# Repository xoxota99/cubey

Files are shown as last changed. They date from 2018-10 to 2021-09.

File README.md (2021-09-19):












# cubey
A Raspberry pi-based Rubik's Cube solving robot.

## Thanks
All credit goes to Jay Flatland, and his [HighFrequencyTwister](https://github.com/jayflatland/HighFrequencyTwister) as the inspiration for this project. This build is just a ghetto version of Jay's project, with a bit of cleaned up documentation, EAGLE files for the relevant PCB, a BOM, and extraneous (to me) stuff removed.

## Hardware
I'm using all the same hardware and 3D-printed parts as [HighFrequencyTwister](https://github.com/jayflatland/HighFrequencyTwister) , but replaced the PC / Arduino combination with a single Raspberry pi. 

I've also created a [custom PCB](https://oshpark.com/shared_projects/dzYt5cpy) to tidy up the wiring of the DRV8825 carrier boards. It sits where a Raspberry pi hat would sit, but definitely does NOT conform to the RPI Hat specification (no cutouts for display connector, no EEPROM for board identification, etc.)

## Software
cubey uses the python implementation of the [kociemba solver](https://github.com/muodov/kociemba), and [piGPIO](https://github.com/joan2937/pigpio) for stepper motor control. Cubey uses a single camera for Cube State estimation, which simplifies calibration, but impacts speed. Cubey definitely *won't* set any world speed records.

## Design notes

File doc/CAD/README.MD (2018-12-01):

STL files (for 3D printing) are in this folder. For the original Fusion 360 files:
- Bottom frame (5 motors): https://a360.co/2QQcA4i
- Top frame (1 motor): https://a360.co/2QOjB5D
- Camera mount / bracket: https://a360.co/2Py3g8A 
- Drill Template: https://a360.co/2qSi3vY
- Stepper Motor Drive Bit: https://a360.co/2PEiVTS

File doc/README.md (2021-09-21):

# Setting Up your Raspberry Pi
These instructions are for Ubuntu 21.04 or later on Raspberry Pi. Other than service setup, they should be applicable to any debian-based, reasonably recent OS (such as Raspbian, or whatever they're calling it now).

## The Basics
Install Ubuntu Server 21.04 or later: https://ubuntu.com/tutorials/how-to-install-ubuntu-on-your-raspberry-pi#1-overview 

SSH into your new, up-and-running RPi using "ubuntu/ubuntu". Change the password.

Create a new user (here we're creating a user "cubey"):

    sudo adduser cubey
    sudo adduser cubey sudo

(Optional) Enable passwordless login: https://linuxize.com/post/how-to-setup-passwordless-ssh-login/ 

SSH into your RPi as the new user you just created.

**Slow SSH logins?** Disable PAM auth: change `UsePAM` from `yes` to `no` in */etc/ssh/sshd_config*

    UsePAM no

(Optional) change the hostname in */etc/hostname*

(Optional) set the timezone: `sudo dpkg-reconfigure tzdata`

(Optional) install zsh: `sudo apt install zsh`

(Optional) set zsh as your default shell: `chsh -s $(which zsh)`

(Optional) install oh-my-zsh: `sh -c "$(curl -fsSL https://raw.github.com/ohmyzsh/ohmyzsh/master/tools/install.sh)"`

Update to latest of everything: 

    sudo apt update
    sudo apt dist-upgrade

Now would be a good time to reboot the RPi (using `sudo reboot`), and reconnect.

## Install Python (3.9):

    sudo apt install -y build-essential python3-setuptools software-properties-common python3.9 python3.9-venv python3.9-dev python3-pip v4l-utils

Set python 3.9 as the default for python3

    cd /usr/bin

    sudo rm aarch64-linux-gnu-python3-config pdb3 pydoc3 pygettext3 python3 python3-config

    sudo sh -c 'ln -s aarch64-linux-gnu-python3.9-config aarch64-linux-gnu-python3-config && \
    ln -s pdb3.9 pdb3 && \
    ln -s pydoc3.9 pydoc3 && \
    ln -s pygettext3.9 pygettext3 && \
    ln -s python3.9 python3 && \
    ln -s python3.9-config python3-config'

## Install OpenCV
    sudo apt install -y python3-opencv

## Install GPIO support
    sudo apt install python3-rpi.gpio python3-lgpio

## Install PIGPio
    cd
    wget https://github.com/joan2937/pigpio/archive/master.zip
    unzip master.zip
    cd pigpio-master
    make
    sudo make install
    sudo touch /lib/systemd/system/pigpiod.service

Add the following to /lib/systemd/system/pigpiod.service:

    [Unit]
    Description=Daemon required to control GPIO pins via pigpio
    [Service]
    ExecStart=/usr/local/bin/pigpiod
    ExecStop=/bin/systemctl kill -s SIGKILL pigpiod
    Type=forking
    [Install]
    WantedBy=multi-user.target

Setup pigpio to run at startup:

    sudo systemctl enable pigpiod

Reboot again, and reconnect.

## Install cubey
    cd
    git clone https://github.com/xoxota99/cubey.git

## Install cubey dependencies: 
    sudo pip install -r cubey/requirements.txt

This includes:
* The [kociemba](https://pypi.org/project/kociemba/) solver library
* [flask](https://flask.palletsprojects.com/en/2.0.x/) web development framework
* [pillow](https://pillow.readthedocs.io/en/stable/) image library.
* [greenlet](https://greenlet.readthedocs.io/en/latest/) concurrent process library
* Prebuilt [OpenCV libraries](https://pypi.org/project/opencv-python/) for python
* Prebuilt [OpenCV addons](https://pypi.org/project/opencv-contrib-python/) for python

## Enable shutdown button and power LED (Optional)
In */boot/firmware/config.txt*, add the following:

    dtoverlay=gpio-poweroff,gpiopin=14
    dtoverlay=gpio-shutdown,gpio_pin=4,active_low=1

and comment out `enable_uart=1`

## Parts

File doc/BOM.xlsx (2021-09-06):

Qty | Description | Link | Unit Price | Total*
1 | Raspberry PI 3 Model B | https://www.amazon.com/dp/B01CD5VC92 | $34.99 | $34.99
2 | Stepper Motor 3-pack | https://www.amazon.com/dp/B00Y2HGJV6 | $26.99 | $53.98
2 | DRV8825 Stepper Motor Driver 5-pack | https://www.amazon.com/dp/B075XH1TSJ | $11.99 | $23.98 | *bulk packs of 5.
1 | 12V Power supply | https://www.amazon.com/dp/B07557XMDQ | $16.80 | $16.80
1 | Power socket | https://www.amazon.com/dp/B06XNMT3WL | $7.49 | $7.49
2 | USB Camera | https://www.amazon.com/dp/B01N07O9CQ | $42.99 | $85.98
1 | AC Power cord | https://www.amazon.com/dp/B07D6MT4L9 | $8.99 | $8.99
1 | Cable wrap / sleeve | https://www.amazon.com/dp/B01MT81WNF | $6.60 | $6.60
1 | Rubik's Cube | https://www.amazon.com/dp/B06XH9Y2XJ | $7.89 | $7.89
1 | 40mm Case fan | https://www.amazon.com/dp/B01CZFUOD0 | $13.98 | $13.98
1 | 40mm fan finger guard grill | https://www.amazon.com/dp/B00D7IH1OK | $5.99 | $5.99
1 | Pololu 5V, 2.5A Step-Down Voltage Regulator D24V22F5 | https://www.pololu.com/product/2858 | $8.95 | $8.95
1 | DRV8825 Stepper Motor PCB | https://oshpark.com/shared_projects/E8F8le0Q | $37.50 | $37.50
1 | Raspbery Pi HAT header | https://www.digikey.com/product-detail/en/te-connectivity-amp-connectors/2-215309-0/A106671-ND/2278517 | $6.12 | $6.12 | For Stepper motor PCB
6 | 100uf Capacitor | https://www.digikey.com/products/en?keywords=P5182-ND | $0.33 | $1.98 | For Stepper motor PCB
1 | terminal blocks 5-pack | https://www.adafruit.com/product/724 | $2.95 | $2.95 | For Stepper motor PCB
Total |  |  |  | $324.17
*Item totals do not include taxes, shipping, customs, etc. YMMV
In addition to the above, you'll ned to 3D-print the actual robot frame.
You'll also need basic tools, soldering iron, screws, wire, etc.
I also laser-cut an acrylic sheet to form the case. That was about $40. Any reasonably sturdy box should do the trick.

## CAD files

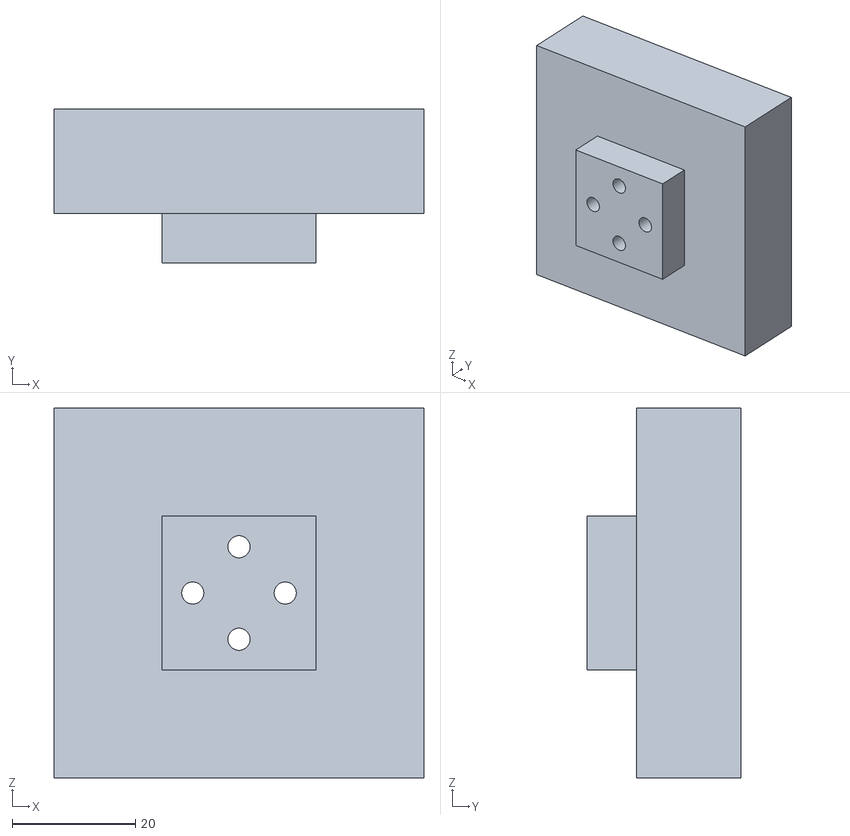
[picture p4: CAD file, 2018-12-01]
doc/CAD/drill_template.stl
60.0 x 25.0 x 60.0

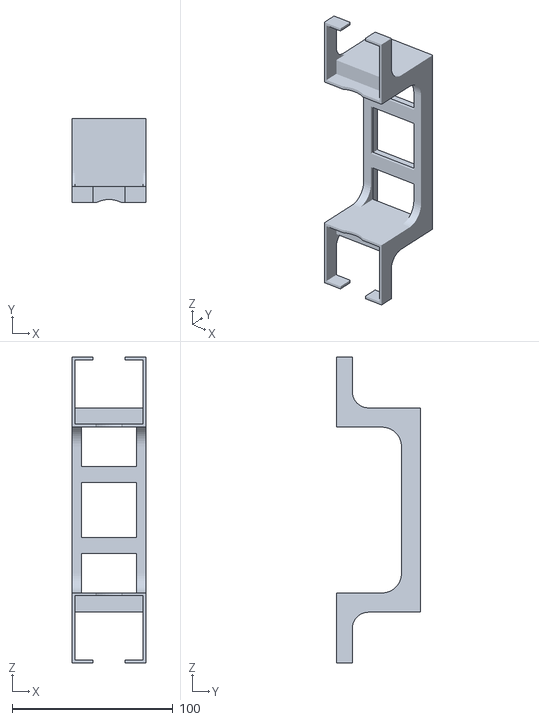
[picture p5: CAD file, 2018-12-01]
doc/CAD/frame_top.stl
46.0 x 52.5 x 190.2

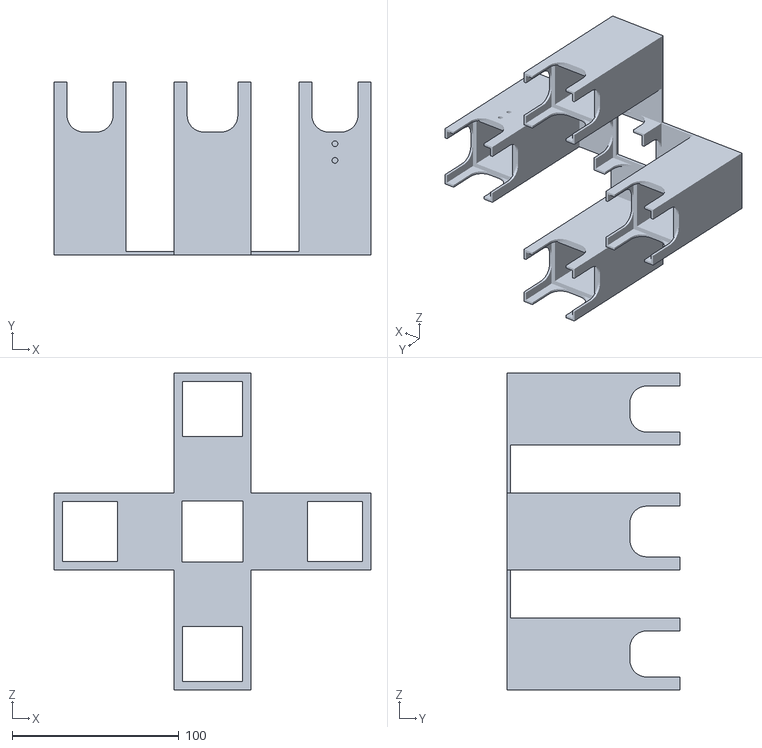
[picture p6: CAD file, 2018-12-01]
doc/CAD/frame_bottom.stl
190.0 x 103.7 x 190.0

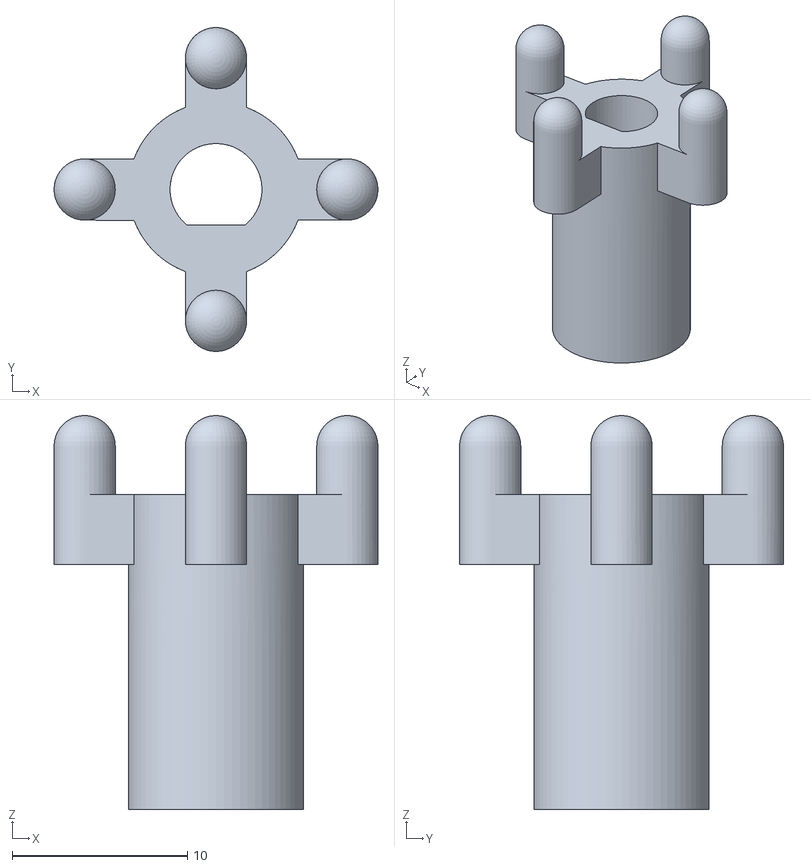
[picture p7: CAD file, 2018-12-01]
doc/CAD/motor_drive_bit.stl
18.5 x 18.5 x 22.5

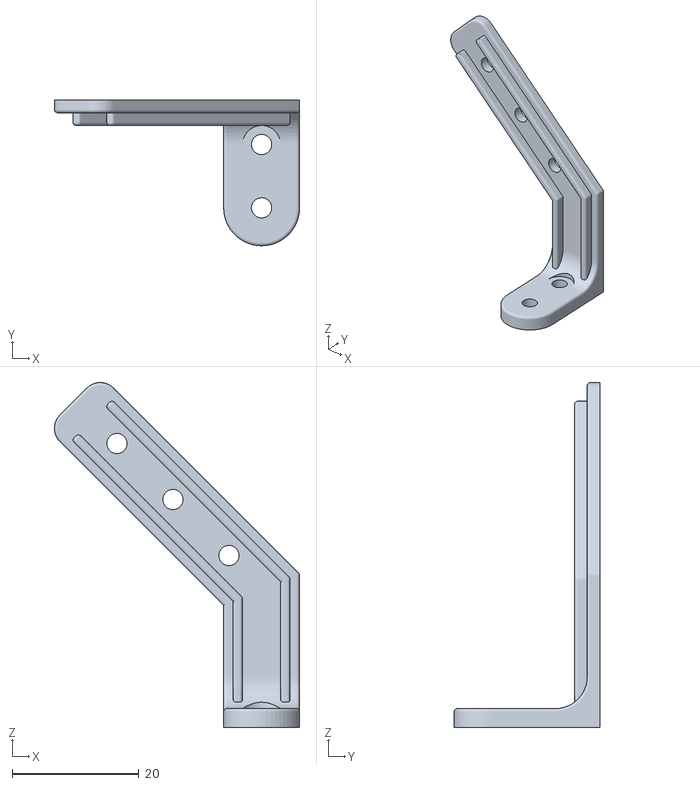
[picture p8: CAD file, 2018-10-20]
doc/CAD/camera_mount.stl
38.7 x 23.0 x 54.5

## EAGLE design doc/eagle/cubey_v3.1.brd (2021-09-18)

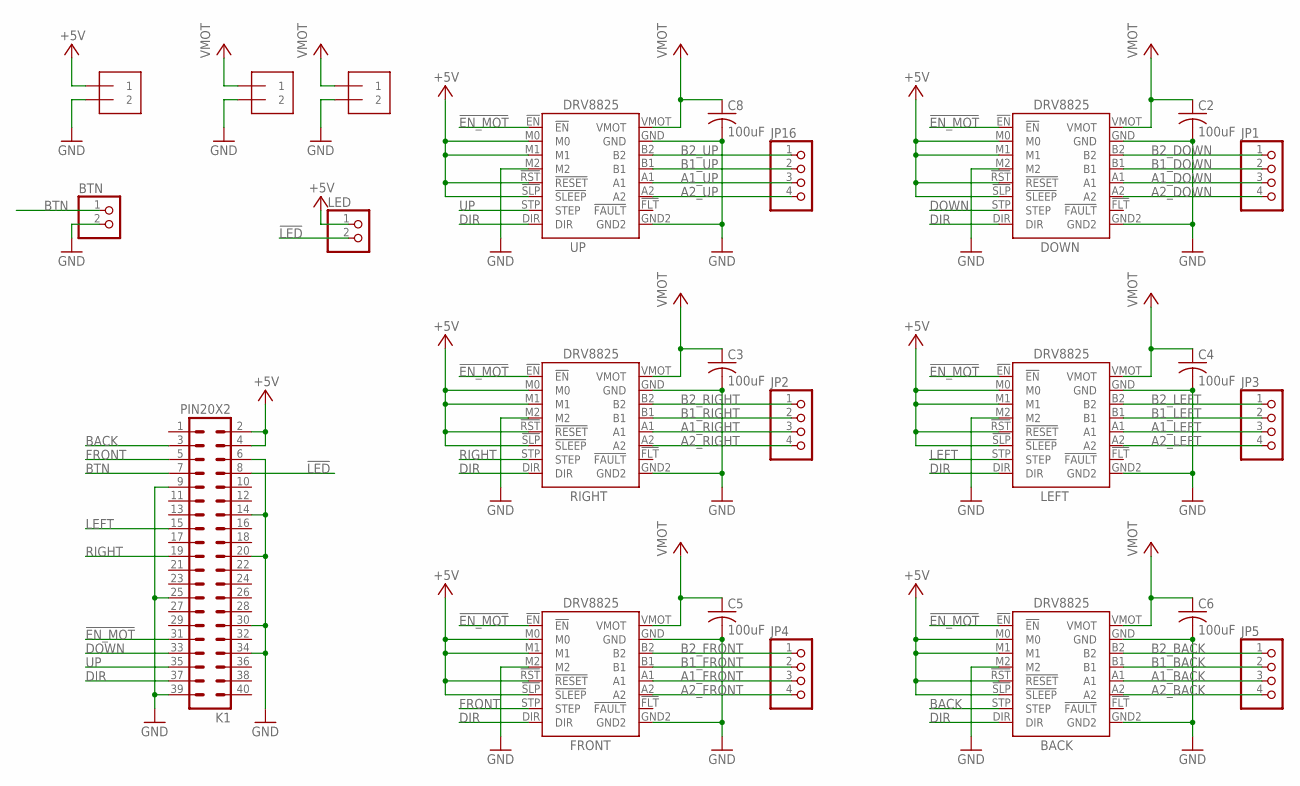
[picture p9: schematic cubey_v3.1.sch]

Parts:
5V_PWR: 1X2-3.5MM
BACK: DRV_8825_SOCKET; DRV_8825_DIP
BTN: PINHD-1X2; 1X02
C2, C3, C4, C5, C6, C8: 100uF; C025-025X050
DOWN: DRV_8825_SOCKET; DRV_8825_DIP
FRONT: DRV_8825_SOCKET; DRV_8825_DIP
JP1, JP2, JP3, JP4, JP5, JP16: PINHD-1X4; 1X04
K1: PIN20X2; PIN_20X2
LED: PINHD-1X2; 1X02
LEFT: DRV_8825_SOCKET; DRV_8825_DIP
MOT_PWR, MOT_PWR1: 1X2-3.5MM
RIGHT: DRV_8825_SOCKET; DRV_8825_DIP
UP: DRV_8825_SOCKET; DRV_8825_DIP

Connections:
!EN_MOT: BACK.!EN, DOWN.!EN, FRONT.!EN, K1.31, LEFT.!EN, RIGHT.!EN, UP.!EN
!LED: K1.8, LED.2
+5V: 5V_PWR.1, BACK.!RST (!RESET), BACK.!SLP (!SLEEP), BACK.M0, BACK.M1, DOWN.!RST (!RESET), DOWN.!SLP (!SLEEP), DOWN.M0, DOWN.M1, FRONT.!RST (!RESET), FRONT.!SLP (!SLEEP), FRONT.M0, FRONT.M1, K1.2, K1.4, LED.1, LEFT.!RST (!RESET), LEFT.!SLP (!SLEEP), LEFT.M0, LEFT.M1, RIGHT.!RST (!RESET), RIGHT.!SLP (!SLEEP), RIGHT.M0, RIGHT.M1, UP.!RST (!RESET), UP.!SLP (!SLEEP), UP.M0, UP.M1
A1_BACK: BACK.A1, JP5.3
A1_DOWN: DOWN.A1, JP1.3
A1_FRONT: FRONT.A1, JP4.3
A1_LEFT: JP3.3, LEFT.A1
A1_RIGHT: JP2.3, RIGHT.A1
A1_UP: JP16.3, UP.A1
A2_BACK: BACK.A2, JP5.4
A2_DOWN: DOWN.A2, JP1.4
A2_FRONT: FRONT.A2, JP4.4
A2_LEFT: JP3.4, LEFT.A2
A2_RIGHT: JP2.4, RIGHT.A2
A2_UP: JP16.4, UP.A2
B1_BACK: BACK.B1, JP5.2
B1_DOWN: DOWN.B1, JP1.2
B1_FRONT: FRONT.B1, JP4.2
B1_LEFT: JP3.2, LEFT.B1
B1_RIGHT: JP2.2, RIGHT.B1
B1_UP: JP16.2, UP.B1
B2_BACK: BACK.B2, JP5.1
B2_DOWN: DOWN.B2, JP1.1
B2_FRONT: FRONT.B2, JP4.1
B2_LEFT: JP3.1, LEFT.B2
B2_RIGHT: JP2.1, RIGHT.B2
B2_UP: JP16.1, UP.B2
BACK: BACK.STP (STEP), K1.3
BTN: BTN.1, K1.7
DIR: BACK.DIR, DOWN.DIR, FRONT.DIR, K1.37, LEFT.DIR, RIGHT.DIR, UP.DIR
DOWN: DOWN.STP (STEP), K1.33
FRONT: FRONT.STP (STEP), K1.5
GND: 5V_PWR.2, BACK.GND, BACK.GND2, BACK.M2, BTN.2, C2.2, C3.2, C4.2, C5.2, C6.2, C8.2, DOWN.GND, DOWN.GND2, DOWN.M2, FRONT.GND, FRONT.GND2, FRONT.M2, K1.6, K1.9, K1.14, K1.20, K1.25, K1.30, K1.34, K1.39, LEFT.GND, LEFT.GND2, LEFT.M2, MOT_PWR.2, MOT_PWR1.2, RIGHT.GND, RIGHT.GND2, RIGHT.M2, UP.GND, UP.GND2, UP.M2
LEFT: K1.15, LEFT.STP (STEP)
RIGHT: K1.19, RIGHT.STP (STEP)
UP: K1.35, UP.STP (STEP)
VMOT: BACK.VMOT, C2.1, C3.1, C4.1, C5.1, C6.1, C8.1, DOWN.VMOT, FRONT.VMOT, LEFT.VMOT, MOT_PWR.1, MOT_PWR1.1, RIGHT.VMOT, UP.VMOT

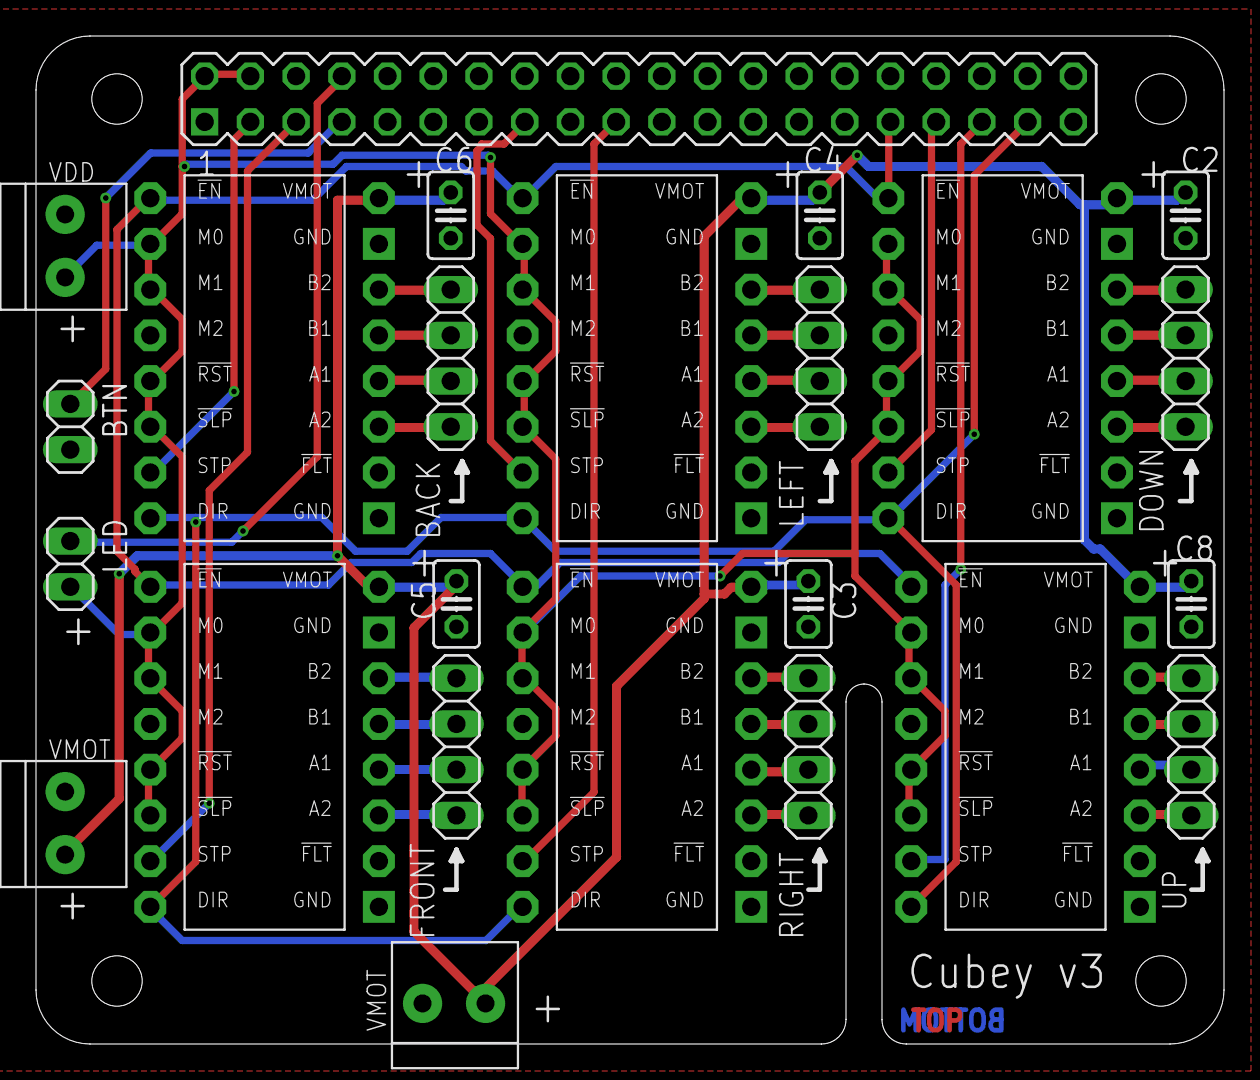
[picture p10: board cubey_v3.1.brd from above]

Board: 2 copper layers, 66.0 x 56.0 mm, 24 parts (0 on the bottom side), 37 nets.

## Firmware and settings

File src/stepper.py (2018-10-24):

from __future__ import division
from time import sleep
import math
import pigpio
from config import cfg

# We are only spinning one motor at a time, so only need one DIR pin.
# (All motors are on the same DIR bus).
pins = cfg['stepper']['pins']
DIR = pins['dir']                # Direction GPIO Pin

UP = pins['up']                  # UP face stepper
RIGHT = pins['right']            # RIGHT face stepper
FRONT = pins['front']            # FRONT face stepper
DOWN = pins['down']              # DOWN face stepper
LEFT = pins['left']              # LEFT face stepper
BACK = pins['back']              # BACK face stepper
DISABLE = 0

if 'disable' in pins:
    DISABLE = pins['disable']

MOTOR_PIN = [UP, RIGHT, FRONT, DOWN, LEFT, BACK]  # Step GPIO Pins
STEP_NAME = ["U", "R", "F", "D", "L", "B"]
STEP_MAP = {
    "U": UP,
    "R": RIGHT,
    "F": FRONT,
    "D": DOWN,
    "L": LEFT,
    "B": BACK
}
RPM = cfg['stepper']['rpm']  # complete revolutions (360 deg.) per minute
# steps per revolution (varies by motor)
STEPS_PER_REVOLUTION = cfg['stepper']['steps_per_rev']
STEPS_PER_DEGREE = STEPS_PER_REVOLUTION / 360.0
STEP_FACTOR = cfg['stepper']['step_factor']
# PULSE_LENGTH_US = 1000000 // (STEPS_PER_REVOLUTION * RPM // 60)
# e.g. 4 revolutions per second = 800 steps per second.
# 800 steps per second = one step every 1250 uS.

MOVE_DELAY = cfg['stepper']['move_delay']

CW = 1
CCW = 0

HERTZ = cfg['stepper']['hertz']

pi = None       # pigpio reference
is_init = False


def _init(force=False):
    """
    _initialize stepper motor frequency / PWM ramps for 90 and 180-degree turns
    """
    global is_init, pi

    # Connect to pigpiod daemon
    pi = pigpio.pi()
    sleep(0.001)

    if force or not is_init:
        if DISABLE:
            pi.set_mode(DISABLE, pigpio.OUTPUT)
            pi.write(DISABLE, 1)

        # Set up pins as an output
        pi.set_mode(DIR, pigpio.OUTPUT)
        for i in MOTOR_PIN:
            pi.set_mode(i, pigpio.OUTPUT)

        is_init = True


def _stop():
    global is_init
    pi.stop()
    sleep(0.001)
    is_init = False


def _tx_pulses(pin, hertz, num, pulse_len=1):
    assert hertz < 500000
    length_us = int(1000000/hertz)
    assert int(pulse_len) < length_us
    assert num < 65536

    if DISABLE:
        pi.write(DISABLE, 0)
        sleep(0.001)       # one millisecond

    num_low = num % 256
    num_high = num // 256

    waveform = []

    waveform.append(pigpio.pulse(1 << pin, 0, pulse_len))
    waveform.append(pigpio.pulse(0, 1 << pin, length_us - pulse_len))

    pi.wave_add_generic(waveform)

    wid = pi.wave_create()

    if wid >= 0:
        pi.wave_chain([255, 0, wid, 255, 1, num_low, num_high])
        while pi.wave_tx_busy():
            pass
        pi.wave_delete(wid)

    if DISABLE:
        pi.write(DISABLE, 1)
        sleep(0.001)       # one millisecond


def rot_90(motor_pin, direction=CW):
    """
    rotate 90 degrees in the specified direction (CW or CCW)
    param:motor_pin - One of UP, RIGHT, FRONT, DOWN, LEFT, or BACK, as defined above.
    param:direction - One of CW or CCW, as defined above.
    """
    if not is_init:
        _init()
    pi.write(DIR, direction)
    _tx_pulses(motor_pin, HERTZ, int(90 * STEPS_PER_DEGREE * STEP_FACTOR))


def rot_180(motor_pin, direction=None):
    """
    rotate 180 degrees in the specified direction (CW or CCW)
    param:motor_pin - One of UP, RIGHT, FRONT, DOWN, LEFT, or BACK, as defined above.
    param:direction - One of CW or CCW, as defined above. Default is CW
    """
    if not is_init:
        _init()
    if direction is not None:
        pi.write(DIR, direction)
    _tx_pulses(motor_pin, HERTZ, int(180 * STEPS_PER_DEGREE * STEP_FACTOR))


def execute(recipe_str):
    """
    Take a recipe, of the form (e.g.) "R L2 F B U' F' D F' U B2 L' U2 B2 U D' B2 U2 L2 D' R2 D2"
    and execute it using the attached stepper motors.
    """
    if not is_init:
        _init()
    recipe = recipe_str.split()
    for step_str in recipe:
        base = step_str[0]
        # TODO: We can execut opposite side simultaneously, if the NEXT item in the list is OPPOSITE this item AND has the SAME orientation (CW or CCW) as this item.
        pin = STEP_MAP[base]
        if (len(step_str) >= 2):
            xtra = step_str[-1:]
            if (xtra == "'"):
                rot_90(pin, CCW)
            elif (xtra == "2"):
                rot_180(pin)
        else:
            rot_90(pin)
        sleep(MOVE_DELAY)
    _stop()


if __name__ == "__main__":
    _init()
    print("Stepper test.")
    delay = MOVE_DELAY

    # rotate each side 90 degrees, four times, with a pause between each rotation.
    for s, mot in zip(STEP_NAME, MOTOR_PIN):
        # s = "U"
        mot = STEP_MAP[s]
        for _ in range(4):
            print(s)
            rot_90(mot, CW)
            sleep(delay)
        for _ in range(4):
            print(s+"'")
            rot_90(mot, CCW)
            sleep(delay)

    # rotate each side twice, 180 degrees, with a pause between each rotation.
    for s, mot in zip(STEP_NAME, MOTOR_PIN):
        for _ in range(2):
            print("2" + s)
            rot_180(mot, CW)
            sleep(delay)
        for _ in range(2):
            print("2"+s+"'")
            rot_180(mot, CCW)
            sleep(delay)

    _stop()

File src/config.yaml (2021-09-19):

app:
  log_level : "INFO"
  log_format : "%(asctime)s - %(levelname)s - %(message)s"

cam:
  warmup_frames : 30
  camera_deviceID : 0

  calibration : "default_calib.yaml"
  
  # When sampling (or scanning) a coordinate in the captured image, average the color from a square 
  # of twice this width / height in pixels.
  sample_aperture: 10 # 20x20 pixel square

  sample_coords: [
      [300, 30], [440, 40],
      [270, 220], [440, 220],
      [270, 430], [420, 440]
    ]

  flip_camera: False
  flip_code: 1       # 0 = vertical flip, 1 for horizontal, -1 for both.


stepper:

  pin_map: # GPIO pin mapping to function.
    back: 2
    front: 3
    left: 22
    right: 10
    disable: 6
    down: 13
    up: 19
    dir: 26

  steps_per_rev: 200
  move_delay: 0.01   # seconds to wait between cube moves.
  hertz: 2000       # pulses per second. Basically speed. Do not exceed 4000 Hz.
  step_factor: 8    # 1/8 microstepping

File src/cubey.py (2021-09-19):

import sys
import logging
import time
import yaml

from lib.motorcontroller import MotorController
from lib.scanner import Scanner
import kociemba

"""
Main Cubey application
"""


def solve(scanner, motors):
    """scan the cube, get a solution from kociemba, then execute it on the robot."""
    logging.info("Scanning...")
    t0 = round(time.time() * 1000)
    state_str = scanner.get_state_string(motors)
    t1 = round(time.time() * 1000)
    logging.info("Scanned state: " + state_str)

    time.sleep(1)

    logging.info("Solving...")
    t2 = round(time.time() * 1000)
    solution = kociemba.solve(state_str)
    t3 = round(time.time() * 1000)
    logging.info("Solution: " + solution)

    logging.info("Executing...\n")
    t4 = round(time.time() * 1000)
    motors.execute(solution)
    t5 = round(time.time() * 1000)

    logging.info('Scan time: {:d}ms'.format(t1 - t0))
    logging.info('Solve time: {:d}ms'.format(t3 - t2))
    logging.info('Execution time: {:d}ms'.format(t5 - t4))

    return(0)


def solve_interactive(scanner, motors):
    """scan the cube, get a solution from kociemba, then execute it on the robot."""
    input("Press any key to begin scanning the cube.")
    t0 = round(time.time() * 1000)
    state_str = scanner.get_state_string(motors)
    t1 = round(time.time() * 1000)
    logging.info("Scan complete! Cube state: {0}\n".format(state_str))

    input("Press any key to generate the solution.")

    t2 = round(time.time() * 1000)
    solution = kociemba.solve(state_str)
    t3 = round(time.time() * 1000)
    logging.info("Finished solving! Solution: {0}\n".format(solution))

    input("Press any key to execute the solution.")

    t4 = round(time.time() * 1000)
    motors.execute(solution)
    t5 = round(time.time() * 1000)

    logging.info('Scan time: {:d}ms'.format(t1 - t0))
    logging.info('Solve time: {:d}ms'.format(t3 - t2))
    logging.info('Execution time: {:d}ms'.format(t5 - t4))

    return(0)


if __name__ == "__main__":
    config_file = "config.yaml"
    config = {}
    with open(config_file, 'r') as ymlfile:
        config = yaml.load(ymlfile, Loader=yaml.FullLoader)

    logging.basicConfig(
        level=logging.getLevelName(config['app']['log_level']), format=config['app']['log_format'])

    scanner = Scanner(config)
    motors = MotorController(config)

    solvers = {
        "DEFAULT": solve,
        "-I": solve_interactive
    }

    mode = "DEFAULT"

    if len(sys.argv) > 1:
        mode = sys.argv[1].upper()

    # non-interactive solver is the default, if not found.
    func = solvers.get(mode, solve)

    sys.exit(func(scanner, motors))

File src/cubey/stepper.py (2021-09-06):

from time import sleep
import pigpio

config = {}
DIR_PIN = 0          # GPIO pin to set direction (cw / ccw)
DISABLE_PIN = 0      # GPIO pin to disable the stepper
FACE_MOTOR_MAP = {}  # map of faces to motor pins.

STEPS_PER_DEGREE = 200  # steps per degree (varies by motor)
STEP_FACTOR = 8  # number of pulses per step. (for microstepping)
MOVE_DELAY = 0.05  # take a small break beween stepper movements.
HERTZ = 400

CW = 0
CCW = 1

pi = None       # pigpio reference
is_init = False


class MotorController:

    def __init__(self, _config):
        global config, DIR_PIN, DISABLE_PIN, FACE_MOTOR_MAP, STEPS_PER_DEGREE, STEP_FACTOR, MOVE_DELAY, HERTZ

        config = _config

        pins = _config['stepper']['pins']

        # Direction GPIO Pin
        DIR_PIN = pins['dir']

        # Disable GPIO pin
        if 'disable' in pins:
            DISABLE_PIN = pins['disable']

        # map of faces to GPIO pins
        FACE_MOTOR_MAP = {
            "U": pins['up'],
            "R": pins['right'],
            "F": pins['front'],
            "D": pins['down'],
            "L": pins['left'],
            "B": pins['back']
        }

        # Number of stepper motor "steps" per degree of angle.
        STEPS_PER_DEGREE = config['stepper']['steps_per_rev'] / 360.0

        # micro-stepping factor.
        STEP_FACTOR = config['stepper']['step_factor']

        # seconds to wait between cube moves.
        MOVE_DELAY = config['stepper']['move_delay']

        HERTZ = config['stepper']['hertz']

    def _initialize(self, force=False):
        """
        _initialize stepper motor frequency / PWM ramps for 90 and 180-degree turns
        """
        global pi, is_init

        # Connect to pigpiod daemon
        pi = pigpio.pi()
        sleep(0.001)

        if force or not is_init:
            if DISABLE_PIN:
                pi.set_mode(DISABLE_PIN, pigpio.OUTPUT)
                pi.write(DISABLE_PIN, 1)

            # Set up pins as an output
            pi.set_mode(DIR_PIN, pigpio.OUTPUT)
            for _, val in config['stepper']['pins'].items():
                pi.set_mode(val, pigpio.OUTPUT)

            is_init = True

    def _stop(self):
        global is_init
        if is_init:
            pi.stop()
            sleep(0.001)
            is_init = False

    def _tx_pulses(self, pin, hertz, num, pulse_len=1):
        assert hertz < 500000
        length_us = int(1000000/hertz)
        assert int(pulse_len) < length_us
        assert num < 65536

        if DISABLE_PIN:
            pi.write(DISABLE_PIN, 0)
            sleep(0.001)       # one millisecond

        num_low = num % 256
        num_high = num // 256

        waveform = []

        waveform.append(pigpio.pulse(1 << pin, 0, pulse_len))
        waveform.append(pigpio.pulse(0, 1 << pin, length_us - pulse_len))

        pi.wave_add_generic(waveform)

        wid = pi.wave_create()

        if wid >= 0:
            pi.wave_chain([255, 0, wid, 255, 1, num_low, num_high])
            while pi.wave_tx_busy():
                pass
            pi.wave_delete(wid)

        if DISABLE_PIN:
            pi.write(DISABLE_PIN, 1)
            sleep(0.001)       # one millisecond

    def rot_90(self, motor_pin, direction=CW):
        """
        rotate 90 degrees in the specified direction (CW or CCW)
        param:motor_pin - One of UP, RIGHT, FRONT, DOWN, LEFT, or BACK, as defined above.
        param:direction - One of CW or CCW, as defined above.
        """
        if not is_init:
            self._initialize()
        pi.write(DIR_PIN, direction)
        steps = int(90 * STEPS_PER_DEGREE * STEP_FACTOR)

        self._tx_pulses(motor_pin, HERTZ, steps)

    def rot_180(self, motor_pin, direction=None):
        """
        rotate 180 degrees in the specified direction (CW or CCW)
        param:motor_pin - One of UP, RIGHT, FRONT, DOWN, LEFT, or BACK, as defined above.
        param:direction - One of CW or CCW, as defined above. Default is CW
        """
        if not is_init:
            self._initialize()
        if direction is not None:
            pi.write(DIR_PIN, direction)
        steps = int(180 * STEPS_PER_DEGREE * STEP_FACTOR)

        self._tx_pulses(motor_pin, HERTZ, steps)

    def execute(self, recipe_str):
        """
        Take a recipe, of the form (e.g.) "R L2 F B U' F' D F' U B2 L' U2 B2 U D' B2 U2 L2 D' R2 D2"
        and execute it using the attached stepper motors.
        """
        # print("EXECUTING....")
        if not is_init:
            self._initialize()
        recipe = recipe_str.split()
        for step_str in recipe:
            base = step_str[0]
            # TODO: We can execute opposite sides simultaneously, if the NEXT item in the list is OPPOSITE this item AND has the SAME orientation (CW or CCW) as this item.
            pin = FACE_MOTOR_MAP[base]
            if (len(step_str) >= 2):
                xtra = step_str[-1:]
                if (xtra == "'"):
                    self.rot_90(pin, CCW)
                elif (xtra == "2"):
                    self.rot_180(pin)
            else:
                self.rot_90(pin)
            sleep(MOVE_DELAY)
        self._stop()

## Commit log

2018-10-15 Initial Commit. Still missing OpenCV / state estimation.
    [Drill Template.stl, Drilled Cube Drive Bit.stl, Five Motor Frame.stl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]
2018-10-16 Added Case design for Raspberry PI and power supply, dimensionanl drawing for camera
2018-10-16 Updated Cube State estimator. Still missing final pixel sampling coordinates in cam.py.
    [cubey.py]
2018-10-16 remove the "tongue" from the board layout. SVG logo.
    [cubey.brd]
2018-10-16 Sample image from front-right camera (60 deg. FOV)
2018-10-19 Added FreeCAD models
    [Drill Template.FCStd, Drilled Cube Drive Bit.FCStd, Five Motor Frame.FCStd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]
2018-10-19 refactor cubey and camera. Add timing instrumentation
2018-10-19 update webstream app to support dual cameras
2018-10-20 Added STL file for the camera mount.
    [Camera Mount.stl]
2018-10-20 deleted unnecessary imges, added basic BOM
    [BOM.xlsx]
2018-10-21 Updated BOM
    [BOM.xlsx]
2018-10-21 Added Solder jumpers for M0, M1 and M2
    [cubey.brd, cubey.sch]
2018-10-21 Simplifying Stepper driver.
2018-10-21 Added test scripts for stepper functinos.
2018-10-21 Updates to delay tables.
    [Delay Table.xlsx]
2018-10-22 New version of DRV8825 carrier, to get around some GPIO issues.
    [cubey_v2.brd, cubey_v2.sch]
2018-10-22 Create a Trim utility script, for moving motors at specific steps.
2018-10-22 Fixed Scramble function, added Cubey v2 pcb pinmap.
    [app.py, config.yaml]
2018-10-22 Minor bugfixes and tweaks
    [stepper.py]
2018-10-24 Rename signals in Cubey PCB design. Finalized V2 with ENABLE pin.
    [cubey.brd, cubey.sch, cubey_v2.brd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]
2018-10-24 Updated BOM with Dubey PCB v2 link
    [BOM.xlsx]
2018-10-24 Added pinouts / wiring diagrams
2018-10-24 Celanup dead code, disable steppers when not in use.
2018-10-24 Fixed color sample coords, added real devices.
    [config.yaml]
2018-10-24 Disable motors when not in use (if the disable pin is defined).
2018-12-01 Update Case Plans SVG
2018-12-01 Restructure / pythonify. Added init.py
    [default_calib.yaml]
2018-12-01 Updated STL files
    [Drill Template.FCStd, Drill Template.stl, Drilled Cube Drive Bit.FCStd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]
2018-12-01 Removed obsolete docs.
    [Delay Table.xlsx, cubey.brd, cubey.sch]
2018-12-01 Added links to Fusion 360 CAD files, updated Cubey PCB EAGLE files.
    [cubey_v2_8step.brd, cubey_v2_8step.sch]
2018-12-02 Fixed config for cubey PCB
    [config.yaml]
2018-12-02 Moved Calibration to a utility script
2018-12-18 Objectify stepper motor control
2018-12-18 move config
    [default_calib.yaml]
2018-12-18 Objectify MotorController
2019-04-12 updated PCB
    [cubey_v3.brd, cubey_v3.sch]
2020-02-11 fixing sonarcloud code smells
    [app.py, calibrate.py, camera.py]
2020-02-11 fixing sonarcloud bugs
2020-02-11 sonarcloud fixes
2020-02-11 Add sonarcloud metrics to readme.md
2020-02-11 reorganization of sonarcloud tags
2021-09-06 Fix config bug (using "B" and "T" instead of "D" and "U")
    [config.yaml]
2021-09-06 General improvements to readability (comments and variable names)
    [default_calib.yaml]
2021-09-06 General improvements to legibility (comments)
    [BOM.xlsx]
2021-09-06 FIX: short-circuit return in get_faces
    [camera.py]
2021-09-06 Code smells (making sonarCloud happy)
2021-09-07 calibration scan efficiency improvement
2021-09-07 fix missing edgelets in scanner
    [scanner.py]
2021-09-07 Add a manual calibration test utility
2021-09-07 Add collision-detect to manual calibration tester.
    [config.yaml]
2021-09-08 more calibration tests
2021-09-08 switch to use HSV instead of RGB for color detection
    [default_calib.yaml]
2021-09-08 fix yaml loading, per https://msg.pyyaml.org/load
    [app.py, calibrate.py, camera.py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]
2021-09-08 making sonarcloud happy
2021-09-08 sonarcloud exclude tests
2021-09-08 refactor / decomplexify for sonarCloud
2021-09-08 bug fixes for __main__
    [scramble.py]
2021-09-08 enable SonarCloud on build.
2021-09-08 sonarcloud config
2021-09-09 Update v3 board layout, with cutout for RPi camera, remove of v2 designs
    [cubey_v2.brd, cubey_v2.sch, cubey_v2_8step.brd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]
2021-09-09 fix special HSV cases (for red)
    [default_calib.yaml]
2021-09-09 remove OYBRWG (color) values, in favor of FURBDL values.
    [default_calib.yaml]
2021-09-09 fix typos in calibration steps
    [calibrate.py]
2021-09-09 reduce complexity in calibration
2021-09-09 reducing complexity of collision detect
    [calibrate.py]
2021-09-09 FIX calibrate
2021-09-09 updated board layout
    [cubey_v3.brd]
2021-09-10 Getting git workflows working for sonarcloud
2021-09-11 remove Sonar project config.
2021-09-11 fix github/sonarcloud integration
2021-09-12 replace print() with logging
    [cubey.py, scramble.py]
2021-09-18 fixes to power net class, adding room for capacitors
    [cubey_v3.1.brd, cubey_v3.1.sch]
2021-09-19 replace logging.warn with logging.warning
    [calibrate.py]
2021-09-19 color bracket config tester
2021-09-19 Slightly improved KeyboardInterrupt, to prevent camera locking up.
    [camera.py]
2021-09-19 fixes to config
    [default_calib.yaml]
